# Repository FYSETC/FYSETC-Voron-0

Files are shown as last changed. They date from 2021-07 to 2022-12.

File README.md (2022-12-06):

# FYSETC-Voron-0.1

This is a project from the VORON community, VORON 0.1. We made a little upgrade and improvement on the basis of this project, and provided a complete set of information. Thanks to the open source materials and support provided by the VORON community, and hope you like it. You can find Voron official information below.

1.VORON 0.1 Official website?¼šhttps://vorondesign.com/voron0.1

2.VORON 0.1 Official Github?¼šhttps://github.com/VoronDesign/Voron-0

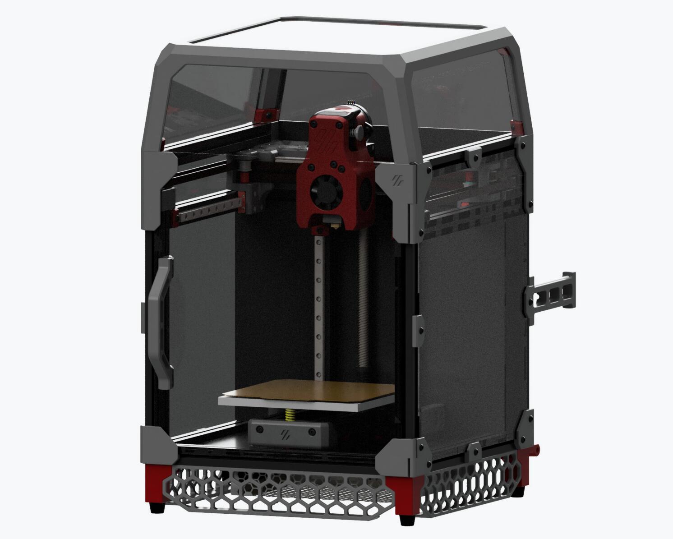
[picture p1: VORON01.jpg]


## 1. Kit advantages:

1?¼‰Using a fully enclosed cabinet design, high-precision finishing anodized custom profile frame, exquisite appearance, can support printing high-temperature consumables, such as: ABS, PC, etc.

2?¼‰Print surface: high-quality powder PEI steel plate, good adhesion, flexibility, easy to take molds; platform: MIC6 aluminum finishing, flatness up to 0.05, attached to high-temperature soft magnetic, and additionally designed positioning pillars, which can be fast Place the steel plate in place and not easily move.

3?¼‰We use 150W genuine brand new Meanwell power supply, which can provide a stable and reliable energy source for the machine and make the machine run more stable. The Raspberry Pi uses TOBSUN 5V 10A DC module for power supply. In addition to providing reliable power for the Raspberry Pi, it also facilitates your other power supply needs, such as cool light strips.

4?¼‰Tornado hotend, check the features [here](https://github.com/FYSETC/FYSETC-Voron-0/blob/main/Tornado_hotend.md). (Please installation guide on our [youtube](https://www.youtube.com/watch?v=a5HArBp4h3s))

5?¼‰Provide a complete set of crimped terminal wires, suitable in length, plug and play, and easy to use.

6?¼‰It adopts high-precision anti-rust linear guide, precise position and stable operation

7?¼‰Using gates belt, wear-resistant, non-slip, long life.

8?¼‰The door handle is fixed with screws, which is more firm and reliable.

9?¼‰Imported silicone thermal mattress, high temperature resistance, built-in over-temperature fuse, high power 24V 75W, fast heating.

10?¼‰High-quality motors.

11?¼‰The use of a 3:1 reduction ratio extruder can increase the extrusion force of the large distance, ensure the smooth and effective extrusion of the consumables, and improve the printing quality.

12?¼‰Use Klipper firmware
Running on [Cheetah V1.2b](https://github.com/FYSETC/FYSETC-Cheetah) (On kit rev 1.0) or [Cheetah v2.0](https://github.com/FYSETC/FYSETC-Cheetah-v2) (On kit rev1.1) and Raspberry Pi 3B+, it can achieve higher printing speed, provide Web control (via WiFi or Ethernet), can connect to a camera, and can be equipped with a 12864 display screen.

## 2. BOM

Check [here](https://github.com/FYSETC/FYSETC-Voron-0/blob/main/BOM.md).

## 3. Modified STLs (2021.07.22)

We update some STLs for the kit. As we found the following issues during the test that 

1.`[a]_Cowling_dragon_x1.stl` fan is difficult to install; 

2.`[a]Mid_Body_Dragon_x1.stl` feed hole is too small; 

3.`Strain_Relief_Spacers_x2.stl` motor uses 20 height; 

4.`Door_Handle_x1 handle.stl` The glue won't stick.

So we modify these STLs base on the originals. You can find them in our `github` or `gitee`.

`[a]_Cowling_dragon_x1.stl` : [github](https://github.com/FYSETC/FYSETC-Voron-0/blob/main/STLs/Toolheads/Mini_Afterburner/Dragon_Toolhead_DD/%5Ba%5D_Cowling_dragon_x1.stl)

`[a]Mid_Body_Dragon_x1.stl`: [github](https://github.com/FYSETC/FYSETC-Voron-0/blob/main/STLs/Toolheads/Mini_Afterburner/Dragon_Toolhead_DD/%5Ba%5D_Mid_Body_Dragon_x1.STL)

`Strain_Relief_Spacers_x2.stl` : [github](https://github.com/FYSETC/FYSETC-Voron-0/blob/main/STLs/Toolheads/Mini_Afterburner/Strain_Relief_Spacers_x2.STL)

`Door_Handle_x1.stl`: [github](https://github.com/FYSETC/FYSETC-Voron-0/blob/main/STLs/Panel_Mounting/Door_Handle_x1.STL)

You can also download these STL files in our `thingiverse` [here](https://www.thingiverse.com/thing:4914152).

## 4. Installation Guide

### 4.1 VORON Assembly manual

Check it [here](https://github.com/VoronDesign/Voron-0/blob/Voron0.1/Manuals/Assembly_Manual_0.1.pdf).

### 4.2 Tornado Hotend installation

Please check it on our [youtube](https://www.youtube.com/watch?v=a5HArBp4h3s).

## 5. Wiring

### 5.1 Rev1.0 kit

Following is our Cheetah v1.2 board wiring diagram for VORON 0.1 rev1.0 kit.

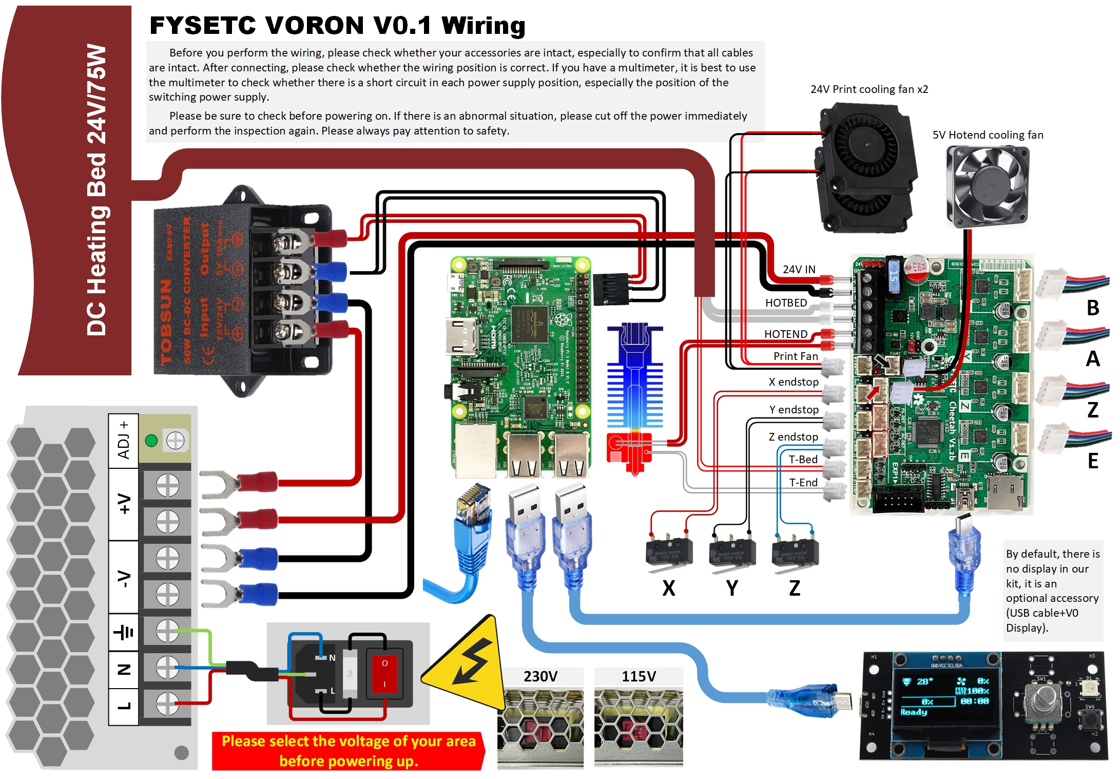
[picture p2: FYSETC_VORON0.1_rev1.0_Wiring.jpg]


We make an example wiring for you, but i think you can do a better job than us. Looking forward to yours, you can share it on VORON discord.



### 5.2 Rev1.1 kit

Following is our Cheetah v2.0 board wiring diagram for VORON 0.1 rev1.1 kit.

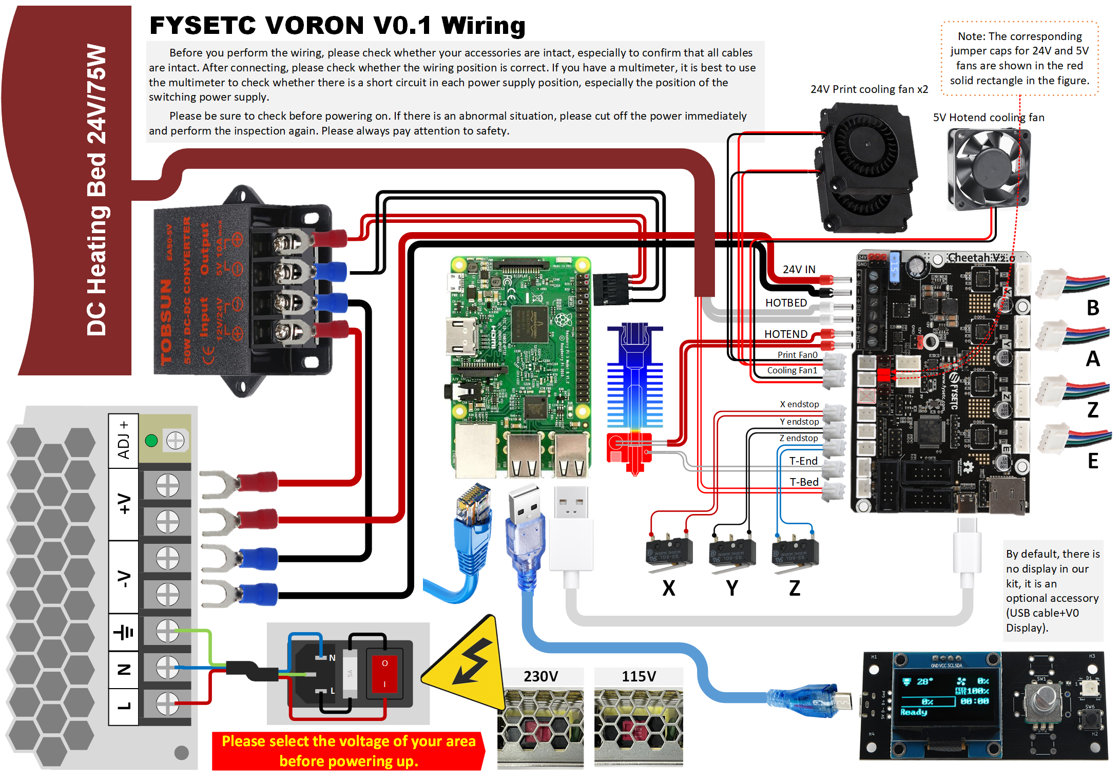
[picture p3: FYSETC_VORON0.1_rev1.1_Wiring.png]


## 6. Firmware&OS

You can check `README.md` in `Firmware&OS` folder beside this `README.md` file [here](https://github.com/FYSETC/FYSETC-Voron-0/tree/main/Firmware&OS). Well we already flashed OS system (on sdcard) and Klipper firmware on Cheetah board for you before the kit leave the factory.

## 7. Community

[Voron community](https://discord.gg/voron)

[FYSETC Facebook group](https://www.facebook.com/groups/238970713918171)

## 8. Buy link

[Aliexpress](https://www.aliexpress.com/item/1005003123492072.html)

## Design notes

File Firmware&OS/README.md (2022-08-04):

# Firmware&OS

## 1. Firmware

### 1.1 Rev 1.0

We use `Cheetah v1.2` motherboard ([github](https://github.com/FYSETC/FYSETC-Cheetah)) for our `Voron-0` rev1.0 kit. And we use `Klipper` firmware. You can get the pre-build firmwares and `printer.cfg` files in folder `rev1.0` next to this `README` file.  In the kit you should find an sdcard with octopi system flashed. After you build your Voron 0.1 machine, you can insert it to the raspberrypi and power up the machine, the machine should work. Remember to connect ethernet cable to raspberrypi and connect Cheetah board to raspberrypi with USB cable.  

#### 1.1.1 Klipper compile

We use the following `make menuconfig` below to compile Klipper. You can check more firmware build information in our Cheetah board github page [here](https://github.com/FYSETC/FYSETC-Cheetah#klipper).

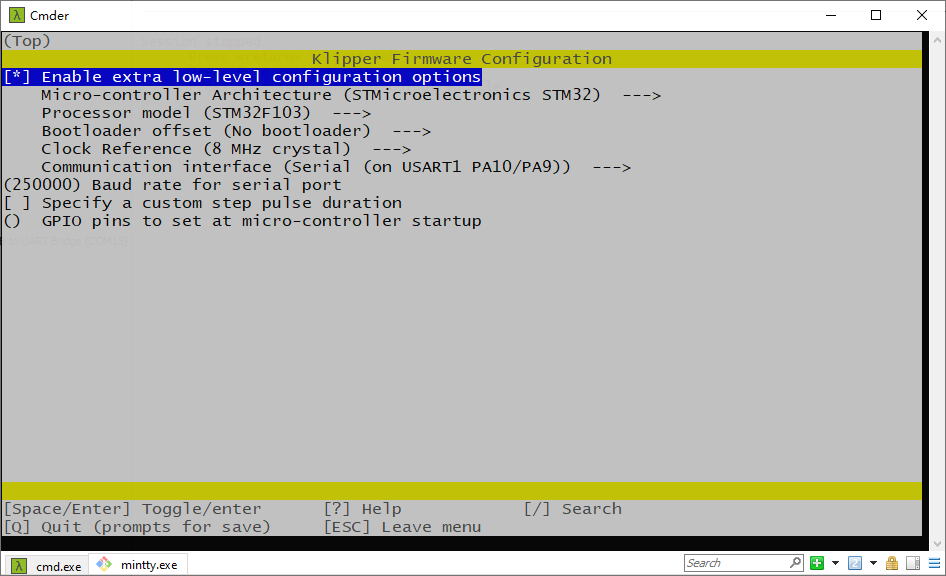
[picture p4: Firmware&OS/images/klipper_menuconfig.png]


#### 1.1.2 How to flash firmware

Well, i don't recommend you to use our pre-build firmwares as klipper firmware always update. I recommend you to compile klipper yours, follow it [here](https://www.klipper3d.org/Installation.html). The prebuild firmwares below just for beginners.

You should power up Cheetah board with 12v/24v power supply first.

##### klipper.bin

If you use our pre-build `klipper.bin` firmware, you can flash the firmware with the command below. This command is also for those who compile klipper yourself, but you need to `cd ~/klpper/out` first. Remember to connect RaspberryPi with usb cable to Cheetah.

```
stm32flash -w klipper.bin -v -i rts,-dtr,dtr /dev/ttyUSB0
```

##### klipper.hex

This is our pre-build firmware in hex format, you can flash it in windows system. 

You can follow the following steps to upload the bootloader.

- Download the flash software in our github https://github.com/FYSETC/STM32Flasher
- Power the board with power supply and connect the board to your PC with USB cable
- Double the click "FlyMcu.exe" software

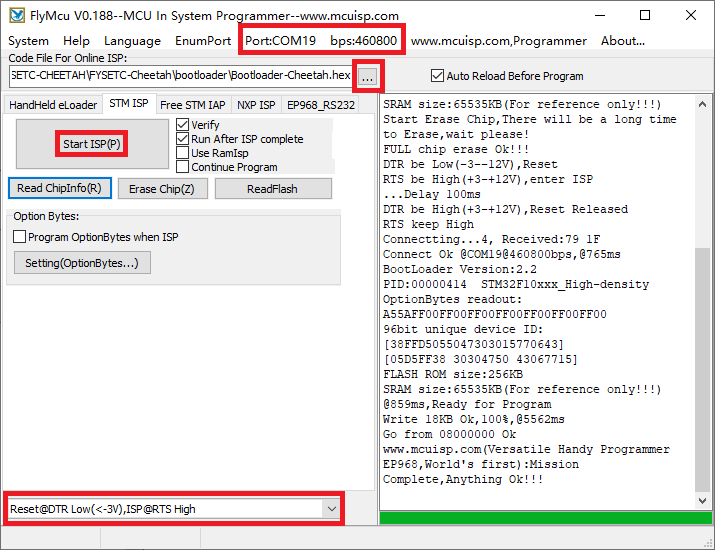
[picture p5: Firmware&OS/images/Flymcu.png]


- Select `Reset@DTR low(<-3v),ISP @RTS High`
- Click "Port" to select the port of your USB
- Select `Bootloader-STM32F103.hex` in the `Code File For Online ISP:` edit box. There is bootloader file named `Bootloader-STM32F103.hex` beside this `README` file.
- At last, click `Start ISP(p)` button to upload the firmware.

#### 1.1.3 printer.cfg

We provide you an example `printer.cfg` in folder `rev1.0` beside this `README` file.

### 1.2 Rev 1.1

We use `Cheetah v2.0` motherboard ([github](https://github.com/FYSETC/FYSETC-Cheetah)) for our `Voron-0` rev1.1 kit. And we use `Klipper` firmware. You can get the pre-build firmwares and `printer.cfg` files in `rev1.1` beside this `README` file.  

#### 1.2.1 Klipper compile

We use the following `make menuconfig` below to compile Klipper. You can check more firmware build information in our Cheetah v2 board github page [here](https://github.com/FYSETC/FYSETC-Cheetah-v2#52-klipper).

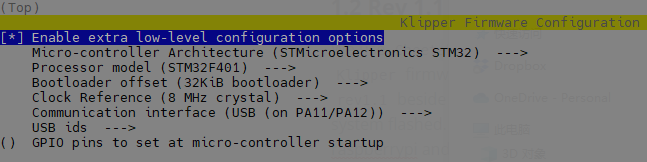
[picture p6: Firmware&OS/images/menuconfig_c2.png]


#### 1.2.2 How to flash firmware

Well, i don't recommend you to use our pre-build firmwares as klipper firmware always update. I recommend you to compile klipper yourself, follow it [here](https://www.klipper3d.org/Installation.html). The pre-build firmwares below just for beginners.

##### klipper.hex

This is our pre-build firmware hex format, follow the instruction [here](https://github.com/FYSETC/FYSETC-Cheetah-v2#533-upload-the-firmwarewindows-dfu) to flash it.

*Note: It is hex file, you don't need to set `Start address` option when using STM32CubeProgrammer.*

Check the klipper version below



##### klipper.bin

32k offset firmware, use the command below to upload the firmware (linux based OS).

```
dfu-util -R -a 0 -s 0x08008000:leave -D klipper.bin
```

#### 1.2.3 printer.cfg

We provide you an example `printer.cfg` in folder `rev1.1` beside this `README` file.

## 2. OS

We provide you two OS images choices: Mainsail OS and Octopi OS.

### 2.1 Mainsail OS

This OS image is only for kit rev1.1 and later, you can get the corresponding Mainsail OS here([1.Dropbox](https://www.dropbox.com/s/669lq3r6z1t4mzo/voron0.1_rpi_cheetah2.0_mainsail.zip?dl=0) [2.百度云盘](https://pan.baidu.com/s/1RYXrs2E_AEZvYQI9CqWZ3w) 提取码：9527) .

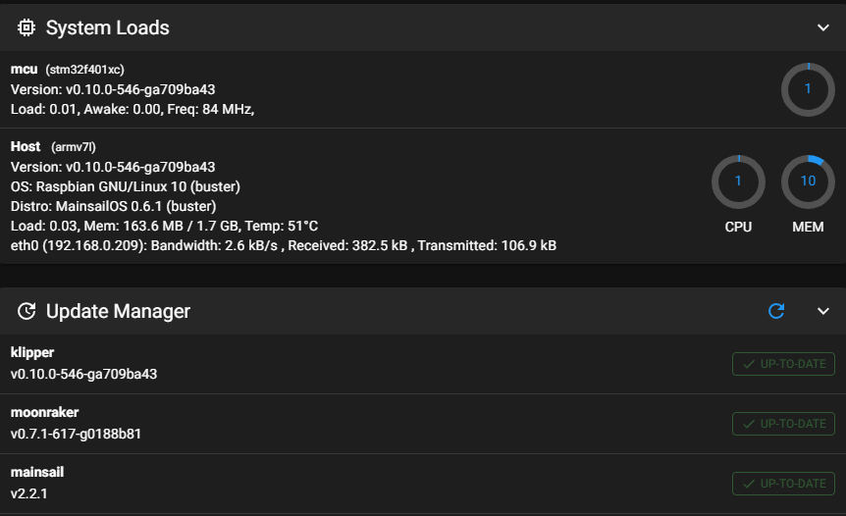
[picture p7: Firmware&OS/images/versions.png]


### 2.2 Octopi OS

If your kit version is rev1.0, then your cheetah board version is 1.2, you can get the corresponding Octopi OS here([1.Dropbox](https://www.dropbox.com/s/o599ni65a6fd2by/voron0.1-cheetah1.2-octopi0.18-octoprint1.6.1-klipper-final.img?dl=0) [2.百度云盘](https://pan.baidu.com/s/1epDDUFP4t6gNax9Bxs07-w) 提取码：1357) . If your kit version is rev1.1, then your cheetah board version is 2.0, and you can get the corresponding Octopi  OS image here([1.Dropbox](https://www.dropbox.com/s/smtbososhue4zym/voron0.1-cheetah2.0-octopi0.18-octoprint1.7.2-klipper.img?dl=0) [2.百度云盘](https://pan.baidu.com/s/12OQ6AqPryXO6TYDF16cSlw ) 提取码：YYDS).

You can login in Octoprint with the following account and password.

```
Account: FYSETC
Password: 12345678
```

### 2.3 How to flash OS image

Before flash, you need an SD card , minimum requirement of SD card capacity is 8G. Please prepare that first. And then you can use this software [here](https://www.balena.io/etcher/) to install. Well that are so many OS flash tool that you can use. And there are a lot of tutorial if you google `how to flash os image`.

### 2.4 SSH account and password

OS SSH account and password

```
Account: pi
Password: raspberry
```

## 3. V0_Display

If you want to install V0_Display to the machine, you should update its firmware first. Please follow `README` in [github](https://gitee.com/fysetc/Voron-Hardware/blob/master/V0_Display/Documentation/Setup_and_Flashing_Guide.md) or [gitee](https://github.com/VoronDesign/Voron-Hardware/blob/master/V0_Display/Documentation/Setup_and_Flashing_Guide.md).

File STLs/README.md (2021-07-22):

# FYSETC-Voron-0.1-STL-update
FYSETC VORON 0.1 STL update part:

Why update: The official original found during the test that 1.[a]_Cowling_dragon_x1 fan is difficult to install; 2.[a]_Mid_Body_x1 feed hole is too small; 3.Strain_Relief_Spacers_x2 motor uses 20 height; 4.Door_Handle_x1 handle The glue won't stick.

1.[a]_Cowling_dragon_x1

2.[a]_Mid_Body_x1

3.Strain_Relief_Spacers_x2

4.Door_Handle_x1

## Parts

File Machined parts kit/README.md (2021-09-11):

# Machined parts kit

If you buy our machined parts kit, you need following STLs to finish your build.

```
Hotbed_wire_harness_clamp.STL
```

```
rear_right_foot.STL
```

Also you can find them in our Thingiverse: https://www.thingiverse.com/thing:4961615

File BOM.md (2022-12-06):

# Package list 

## Revision 1.0

| Index | Sort | Component | Qty | Note |
| ----- | :--- | --- | --- | --- |
| 1 | Fasteners | Voron V0.1 fasteners Pack | 1 SET  | |
| 2 | Extruder Hardware | BMG Extruder gear kit(Includes all accessories) | 1 SET  | |
| 3 | Frame | Voron 0.1 1515 aluminum extrusion profile frame kit | 19 PCS | |
| 4 | Electronics | Meanwell LRS-150-24 | 1 PC | |
| 5 | Electronics | Buck converter - 24V to 5V | 1 PC | |
| 6 | Electronics | FYSETC  cheetah 1.2 | 1 PC | |
| 7 | Electronics | Raspberry Pi 3B+ | 1 PC | |
| 8 | Electronics | MicroSD Card 8G | 1 PC | |
| 9 | Electronics | NEMA14 Stepper Motor 40Ncm 35HSH7402-24B-400A(check [here](https://github.com/FYSETC/FYSETC-MOTORS/tree/main/35HSH7402-24B-400A)) | 2 PCS  | |
| 10 | Electronics | NEMA17 Stepper Motor (34mm max) with integrated lead screw 200mm T8x8 42HSC1404B-200N8(check [here](https://github.com/FYSETC/FYSETC-MOTORS/tree/main/42HSC1404B-200N8)) | 1 PC | |
| 11 | Electronics | NEMA14 36mm round pancake Stepper Motor with 10 tooth spur gear G36HSY4407-6D-550(check [here](https://github.com/FYSETC/FYSETC-MOTORS/tree/main/G36HSY4407-6D-550)) | 1 PCS  | |
| 12 | Electronics | 3010 blower fans 24V | 1 PC | |
| 13 | Electronics | 3007 axial fan 5V (min 3.5CFM) | 1 PC | |
| 14 | Electronics | Micro Switch（With wire） | 3 PCS  | |
| 15 | Electronics | C13 Power Cord | 1 PC | |
| 16 | Electronics | AC Inlet （ With Fuse ） | 1 SET  | |
| 17 | Electronics | Tornodo hotend（ Both all-metal and PTFE heatbreak included） | 1 PC | |
| 18 | Electronics | 24V Heater Cartridge (slim wires) | 1 PC | |
| 19 | Electronics | Thermistor for your hotend of choice | 1 PC | |
| 20 | Electronics | VHB tape (20mm) | 1 PC | |
| 21 | Cables | VORON 0.1 cables kit（All cables are connected to the terminals，Plug and play） | 1 SET  | |
| 22 | Cables | 2mmx120mm zip ties | 20 PCS | |
| 23 | Cables | Network cable | 1 PC | |
| 24 | Motion | F623-RS Bearing | 24 PCS | |
| 25 | Motion | MGN7H Linear Rail with Carriage (150mm) | 5 PCS  | |
| 26 | Motion | GT2 20T (6mm wide) (5mm bore) | 2 PCS  | |
| 27 | Motion | GATES-LL-GT2 Open Belt 6mm (3 meters) | 1 PC | |
| 28 | Motion | T8 flange Nut 8mm Lead --anti-backlash | 1 PC | |
| 29 | Buildplate | Aluminum Build Plate (MIC6) 120x120mm | 1 PC | Positionable steel plate like prusa |
| 30 | Buildplate | Silicone DC 24V Heater 100x100mm 75W （Faster heating rate，Fuse inside） | 1 PC | |
| 31 | Buildplate | Yellow die springs 8x4x20mm | 3 PCS  | |
| 32 | Buildplate | PEI Powder Coated Spring Steel Flex Buildplate 120x120mm | 1 PC | |
| 33 | Buildplate | Magnetic sheet for spring steel plate 120x120mm | 1 PC | |
| 34 | Panels | VORON 0.1 Acrylic Panels kit | 1 SET  | |
| 35 | Bowden | Bowden Fitting ECAS04 | 1 PC | |
| 36 | Bowden | Bowden Tubing 4mmOD 1.9mmID (1.5 meter) | 1 PC | |
| 37 | Misc | Little Rubber Feet (14x11x9mm) | 4 PCS  | |
| 38 | Misc | 6mm x 3mm Round Neodymium Magnets | 8 PCS  | |
| 39 | Misc | Weaving casing φ8mm length 300mm | 1 SET  | Replace one tank chain |
| 40 | Misc | Weaving casing φ8mm length 350mm | 1 SET  | |
| 41 | Misc | FYSETC label | 1 PC | |
| 42 | Tools | Cutting pliers | 1 SET  | |
| 43 | Tools | Hexagonal wrenchs | 1 PC | |
| 44 | Tools | Thermal silica | 1 PC | |
| 45 | Tools | FYSETC VORON V0.1 Wiring manual | 1 SET  | |

## Revision 1.1

| Index | Sort | Component | Qty | Note |
| ----- | :--- | --- | --- | --- |
| 1 | Fasteners | Voron V0.1 fasteners Pack | 1 SET  | v1.1 add Motor Spacer |
| 2 | Extruder Hardware | BMG Extruder gear kit(Includes all accessories) | 1 SET  | |
| 3 | Frame | Voron 0.1 1515 aluminum extrusion profile frame kit | 19 PCS | |
| 4 | Electronics | Meanwell LRS-150-24 | 1 PC | |
| 5 | Electronics | Buck converter - 24V to 5V | 1 PC | |
| 6 | Electronics | FYSETC  cheetah 2.0 | 1 PC | v1.1 Upgrade to 2.0 |
| 7 | Electronics | Raspberry Pi 3B+ | 1 PC | |
| 8 | Electronics | MicroSD Card 8G | 1 PC | |
| 9 | Electronics | NEMA14 Stepper Motor 40Ncm 35HSH7402-24B-400A(check [here](https://github.com/FYSETC/FYSETC-MOTORS/tree/main/35HSH7402-24B-400A)) Teflon wire | 2 PCS  | v1.1 upgraded to Teflon line |
| 10 | Electronics | NEMA17 Stepper Motor (34mm max) with integrated lead screw 200mm T8x8 42HSC1404B-200N8(check [here](https://github.com/FYSETC/FYSETC-MOTORS/tree/main/42HSC1404B-200N8)) Teflon wire | 1 PC | v1.1 upgraded to Teflon line |
| 11 | Electronics | NEMA14 36mm round pancake Stepper Motor with 10 tooth spur gear G36HSY4407-6D-550(check [here](https://github.com/FYSETC/FYSETC-MOTORS/tree/main/G36HSY4407-6D-550)) Teflon wire | 1 PCS  | v1.1 upgraded to Teflon line |
| 12 | Electronics | 3010 blower fans 24V | 1 PC | v1.1 upgraded to Teflon line |
| 13 | Electronics | 3007 axial fan 5V (min 3.5CFM) | 1 PC | v1.1 upgraded to Teflon line |
| 14 | Electronics | Micro Switch（With wire） | 3 PCS  | v1.1 upgraded to Teflon line |
| 15 | Electronics | C13 Power Cord | 1 PC | |
| 16 | Electronics | AC Inlet （ With Fuse ） | 1 SET  | |
| 17 | Electronics | Tornodo hotend（ Both all-metal and PTFE heatbreak included） | 1 PC | |
| 18 | Electronics | 24V Heater Cartridge (slim wires) | 1 PC | |
| 19 | Electronics | Thermistor for your hotend of choice | 1 PC | |
| 20 | Electronics | VHB tape (20mm) | 1 PC | |
| 21 | Cables | VORON 0.1 cables kit（All cables are connected to the terminals，Plug and play） | 1 SET  | v1.1 upgraded to Teflon line |
| 22 | Cables | 2mmx120mm zip ties | 20 PCS | |
| 23 | Cables | Network cable | 1 PC | |
| 24 | Cables | Type-C line | 1 PC | v1.1 upgraded to elbow |
| 25 | Motion | F623-RS Bearing | 24 PCS | |
| 26 | Motion | MGN7H Linear Rail with Carriage (150mm) | 5 PCS  | |
| 27 | Motion | GT2 20T (6mm wide) (5mm bore) | 2 PCS  | |
| 28 | Motion | GATES-LL-GT2 Open Belt 6mm (3 meters) | 1 PC | |
| 29 | Motion | T8 flange Nut 8mm Lead --anti-backlash | 1 PC | |
| 30 | Buildplate | Aluminum Build Plate (MIC6) 120x120mm | 1 PC | Positionable steel plate like prusa |
| 31 | Buildplate | Silicone DC 24V Heater 100x100mm 75W （Faster heating rate，Fuse inside） | 1 PC | |
| 32 | Buildplate | Thermal Fuse (125C) | 1 PC | |
| 33 | Buildplate | Yellow die springs 8x4x20mm | 3 PCS  | |
| 34 | Buildplate | PEI Powder Coated Spring Steel Flex Buildplate 120x120mm | 1 PC | |
| 35 | Buildplate | Magnetic sheet for spring steel plate 120x120mm | 1 PC | |
| 36 | Panels | VORON 0.1 Acrylic Panels kit | 1 SET  | |
| 37 | Bowden | Bowden Fitting ECAS04 | 2 PC | v1.1 added 1PC |
| 38 | Bowden | Bowden Tubing 4mmOD 1.9mmID (1.5 meter) | 1 PC | |
| 39 | Misc | Tank Chain 7x7mm | 1 PC | v1.1 added |
| 39 | Misc | Little Rubber Feet (14x11x11mm) | 4 PCS  | v1.1 `2mm` taller than v1.0 |
| 40 | Misc | XH2.54 2/3/4 Pin Plastic shell | 1 SET  | v1.1 added |
| 41 | Misc | 6mm x 3mm Round Neodymium Magnets | 8 PCS  | |
| 42 | Misc | Weaving casing φ8mm length 300mm | 1 SET  | |
| 43 | Misc | Weaving casing φ8mm length 350mm | 1 SET  | |
| 44 | Misc | FYSETC label | 1 PC | |
| 45 | Tools | Cutting pliers | 1 SET  | |
| 46 | Tools | Hexagonal wrenchs | 1 PC | |
| 47 | Tools | Thermal silica | 1 PC | |
| 48 | Tools | FYSETC VORON V0.1 Wiring manual | 1 SET  | |
## Revision 1.2

| Index | Sort | Component | Qty | Note |
| ----- | :--- | --- | --- | --- |
| 1 | Fasteners | Voron V0.1 fasteners Pack | 1 SET  | v1.1 add Motor Spacer |
| 2 | Extruder Hardware | BMG Extruder gear kit(Includes all accessories) | 1 SET  | |
| 3 | Frame | Voron 0.1 1515 aluminum extrusion profile frame kit | 19 PCS | |
| 4 | Electronics | Meanwell LRS-150-24 | 1 PC | |
| 5 | Electronics | Buck converter - 24V to 5V | 1 PC | |
| 6 | Electronics | FYSETC  cheetah 2.0 | 1 PC | v1.1 Upgrade to 2.0 |
| 7 | Electronics | Raspberry Pi 4B 2GB | 1 PC | V1.2 Optional |
| 8 | Electronics | MicroSD Card 8G | 1 PC | |
| 9 | Electronics | NEMA14 Stepper Motor 40Ncm 35HSH7402-24B-400A(check [here](https://github.com/FYSETC/FYSETC-MOTORS/tree/main/35HSH7402-24B-400A)) Teflon wire | 2 PCS  | v1.1 upgraded to Teflon line |
| 10 | Electronics | NEMA17 Stepper Motor (34mm max) with integrated lead screw 200mm T8x8 42HSC1404B-200N8(check [here](https://github.com/FYSETC/FYSETC-MOTORS/tree/main/42HSC1404B-200N8)) Teflon wire | 1 PC | v1.1 upgraded to Teflon line |
| 11 | Electronics | NEMA14 36mm round pancake Stepper Motor with 10 tooth spur gear G36HSY4407-6D-550(check [here](https://github.com/FYSETC/FYSETC-MOTORS/tree/main/G36HSY4407-6D-550)) Teflon wire | 1 PCS  | v1.1 upgraded to Teflon line |
| 12 | Electronics | 3010 blower fans 24V | 1 PC | v1.1 upgraded to Teflon line |
| 13 | Electronics | 3007 axial fan 5V (min 3.5CFM) | 1 PC | v1.1 upgraded to Teflon line |
| 14 | Electronics | Micro Switch（With wire） | 3 PCS  | v1.1 upgraded to Teflon line |
| 15 | Electronics | C13 Power Cord | 1 PC | |
| 16 | Electronics | AC Inlet （ With Fuse ） | 1 SET  | v1.2 Wiring color changes |
| 17 | Electronics | Tornodo hotend（ Both all-metal and PTFE heatbreak included） | 1 PC | |
| 18 | Electronics | 24V Heater Cartridge (slim wires) | 1 PC | |
| 19 | Electronics | Thermistor for your hotend of choice | 1 PC | |
| 20 | Electronics | VHB tape (20mm) | 1 PC | |
| 21 | Cables | VORON 0.1 cables kit（All cables are connected to the terminals，Plug and play，Label buckle） | 1 SET  | v1.1 upgraded to Teflon line  v1.2 add Label buckle |
| 22 | Cables | 2mmx120mm zip ties | 20 PCS | |
| 23 | Cables | Network cable | 1 PC | |
| 24 | Cables | Type-C line | 1 PC | v1.1 upgraded to elbow |
| 25 | Motion | F623-RS Bearing | 24 PCS | |
| 26 | Motion | MGN7H Linear Rail with Carriage (150mm) | 5 PCS  | |
| 27 | Motion | GT2 20T (6mm wide) (5mm bore) | 2 PCS  | |
| 28 | Motion | GATES-LL-GT2 Open Belt 6mm (3 meters) | 1 PC | |
| 29 | Motion | T8 flange Nut 8mm Lead --anti-backlash | 1 PC | |
| 30 | Buildplate | Aluminum Build Plate (MIC6) 120x120mm | 1 PC | Positionable steel plate like prusa |
| 31 | Buildplate | Silicone DC 24V Heater 100x100mm 75W （Faster heating rate，Fuse inside） | 1 PC | |
| 32 | Buildplate | Thermal Fuse (125C) | 1 PC | |
| 33 | Buildplate | Yellow die springs 8x4x20mm | 3 PCS  | |
| 34 | Buildplate | PEI Powder Coated Spring Steel Flex Buildplate 120x120mm | 1 PC | |
| 35 | Buildplate | Magnetic sheet for spring steel plate 120x120mm | 1 PC | |
| 36 | Panels | VORON 0.1 Acrylic Panels kit | 1 SET  | |
| 37 | Bowden | Bowden Fitting ECAS04 | 2 PC | v1.1 added 1PC |
| 38 | Bowden | Bowden Tubing 4mmOD 1.9mmID (1.5 meter) | 1 PC | |
| 39 | Misc | Tank Chain 7x7mm | 1 PC | v1.1 added |
| 39 | Misc | Little Rubber Feet (14x11x11mm) | 4 PCS  | v1.1 taller than v1.0 |
| 40 | Misc | XH2.54 2/3/4 Pin Plastic shell | 1 SET  | v1.1 added |
| 41 | Misc | 6mm x 3mm Round Neodymium Magnets | 8 PCS  | |
| 42 | Misc | Weaving casing φ8mm length 300mm | 1 SET  | |
| 43 | Misc | Weaving casing φ8mm length 350mm | 1 SET  | |
| 44 | Misc | FYSETC label | 1 PC | |
| 45 | Tools | Cutting pliers | 1 SET  | |
| 46 | Tools | Hexagonal wrenchs | 1 PC | |
| 47 | Tools | Thermal silica | 1 PC | |
| 48 | Tools | FYSETC VORON V0.1 Wiring manual | 1 SET  | |
## Revision 1.3

| Index | Sort | Component | Qty | Note |
| ----- | :--- | --- | --- | --- |
| 1 | Fasteners | Voron V0.1 fasteners Pack | 1 SET  | v1.1 add Motor Spacer |
| 2 | Extruder Hardware | BMG Extruder gear kit(Includes all accessories) | 1 SET  | |
| 3 | Frame | Voron 0.1 1515 aluminum extrusion profile frame kit | 19 PCS | |
| 4 | Electronics | Meanwell LRS-150-24 | 1 PC | |
| 5 | Electronics | Buck converter - 24V to 5V | 1 PC | |
| 6 | Electronics | FYSETC  cheetah 2.0 | 1 PC | v1.1 Upgrade to 2.0 |
| 7 | Electronics | Raspberry Pi 4B 2GB | 1 PC | V1.2 Optional |
| 8 | Electronics | MicroSD Card 8G | 1 PC | |
| 9 | Electronics | NEMA14 Stepper Motor 40Ncm 35HSH7402-24B-400A(check [here](https://github.com/FYSETC/FYSETC-MOTORS/tree/main/35HSH7402-24B-400A)) Teflon wire | 2 PCS  | v1.1 upgraded to Teflon line |
| 10 | Electronics | NEMA17 Stepper Motor (34mm max) with integrated lead screw 200mm T8x8 42HSC1404B-200N8(check [here](https://github.com/FYSETC/FYSETC-MOTORS/tree/main/42HSC1404B-200N8)) Teflon wire | 1 PC | v1.1 upgraded to Teflon line |
| 11 | Electronics | NEMA14 36mm round pancake Stepper Motor with 10 tooth spur gear G36HSY4407-6D-550(check [here](https://github.com/FYSETC/FYSETC-MOTORS/tree/main/G36HSY4407-6D-550)) Teflon wire | 1 PCS  | v1.1 upgraded to Teflon line |
| 12 | Electronics | 3010 blower fans 24V | 1 PC | v1.1 upgraded to Teflon line |
| 13 | Electronics | 3007 axial fan 5V (min 3.5CFM) | 1 PC | v1.1 upgraded to Teflon line |
| 14 | Electronics | Micro Switch（With wire） | 3 PCS  | v1.1 upgraded to Teflon line |
| 15 | Electronics | C13 Power Cord | 1 PC | |
| 16 | Electronics | AC Inlet （ With Fuse ） | 1 SET  | v1.2 Wiring color changes |
| 17 | Electronics | Tornodo hotend（ Both all-metal and PTFE heatbreak included） | 1 PC | |
| 18 | Electronics | 24V Heater Cartridge (slim wires) | 1 PC | |
| 19 | Electronics | Thermistor for your hotend of choice | 1 PC | |
| 20 | Electronics | VHB tape (20mm) | 1 PC | |
| 21 | Cables | VORON 0.1 cables kit（All cables are connected to the terminals，Plug and play，Label buckle） | 1 SET  | v1.1 upgraded to Teflon line  v1.2 add Label buckle |
| 22 | Cables | 2mmx120mm zip ties | 20 PCS | |
| 23 | Cables | Network cable | 1 PC | |
| 24 | Cables | Type-C line | 1 PC | v1.1 upgraded to elbow |
| 25 | Motion | F623-RS Bearing | 24 PCS | |
| 26 | Motion | MGN7H Linear Rail with Carriage (150mm) | 5 PCS  | v1.3 upgraded to  Stainless steel |
| 27 | Motion | GT2 20T (6mm wide) (5mm bore) | 2 PCS  | |
| 28 | Motion | GATES-LL-GT2 Open Belt 6mm (3 meters) | 1 PC | |
| 29 | Motion | T8 flange Nut 8mm Lead --anti-backlash | 1 PC | |
| 30 | Buildplate | Aluminum Build Plate (MIC6) 120x120mm | 1 PC | Positionable steel plate like prusa |
| 31 | Buildplate | Silicone DC 24V Heater 100x100mm 75W （Faster heating rate，Fuse inside） | 1 PC | |
| 32 | Buildplate | Thermal Fuse (125C) | 1 PC | |
| 33 | Buildplate | Yellow die springs 8x4x20mm | 3 PCS  | |
| 34 | Buildplate | PEI Powder Coated Spring Steel Flex Buildplate 120x120mm | 1 PC | |
| 35 | Buildplate | Magnetic sheet for spring steel plate 120x120mm | 1 PC | |
| 36 | Panels | VORON 0.1 Acrylic Panels kit | 1 SET  | |
| 37 | Bowden | Bowden Fitting ECAS04 | 2 PC | v1.1 added 1PC |
| 38 | Bowden | Bowden Tubing 4mmOD 1.9mmID (1.5 meter) | 1 PC | |
| 39 | Misc | Tank Chain 7x7mm | 1 PC | v1.1 added |
| 39 | Misc | Little Rubber Feet (14x11x11mm) | 4 PCS  | v1.1 taller than v1.0 |
| 40 | Misc | XH2.54 2/3/4 Pin Plastic shell | 1 SET  | v1.1 added |
| 41 | Misc | 6mm x 3mm Round Neodymium Magnets | 8 PCS  | |
| 42 | Misc | Weaving casing φ8mm length 300mm | 1 SET  | |
| 43 | Misc | Weaving casing φ8mm length 350mm | 1 SET  | |
| 44 | Misc | FYSETC label | 1 PC | |
| 45 | Tools | Cutting pliers | 1 SET  | |
| 46 | Tools | Hexagonal wrenchs | 1 PC | |
| 47 | Tools | Thermal silica | 1 PC | |
| 48 | Tools | FYSETC VORON V0.1 Wiring manual | 1 SET  | |

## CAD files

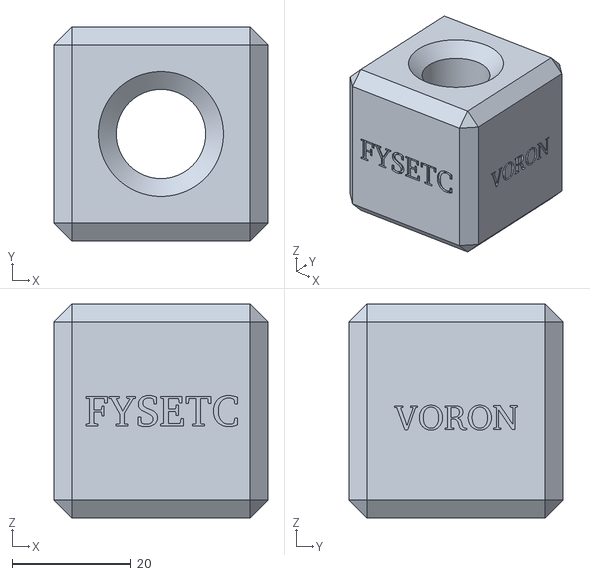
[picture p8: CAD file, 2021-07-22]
FYSETC VORON Cube.STL
36.0 x 36.0 x 36.0

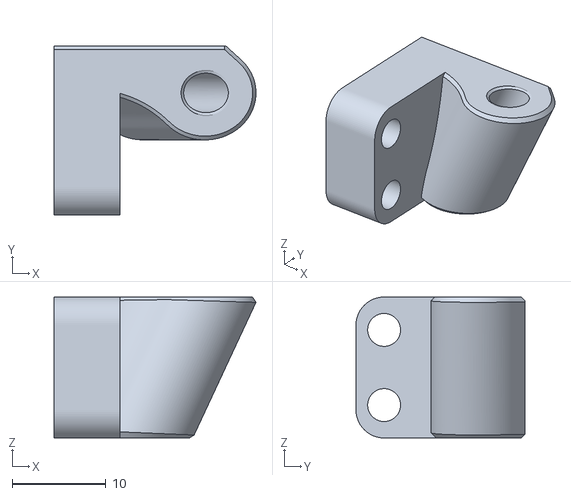
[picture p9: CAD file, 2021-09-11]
Machined parts kit/rear_right_foot.STL
21.5 x 18.0 x 15.0

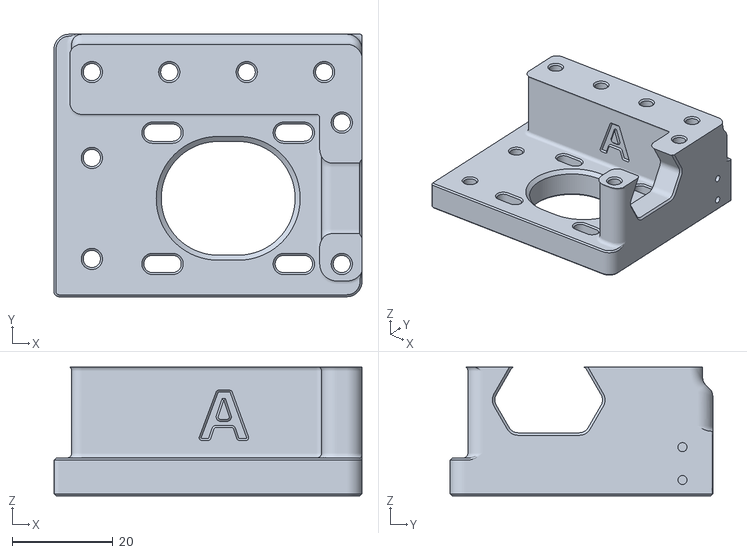
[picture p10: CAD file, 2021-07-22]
STLs/A_Drive_Frame_Lower_x1.stl
61.0 x 52.0 x 25.5

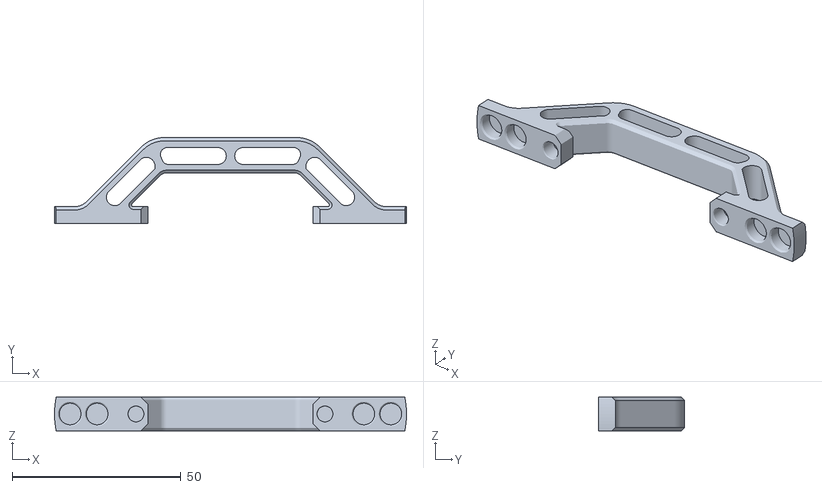
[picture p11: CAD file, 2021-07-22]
STLs/Panel_Mounting/Door_Handle_x1.STL
104.3 x 25.5 x 10.0

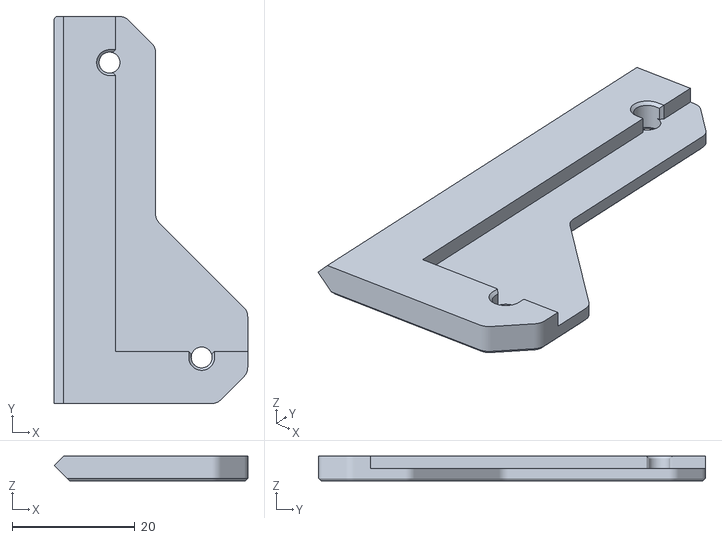
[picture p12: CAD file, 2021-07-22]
STLs/Panel_Mounting/For_2mm_Panels/2mm_Top_Corner_Side_mirror_x1.STL
31.5 x 63.0 x 4.00

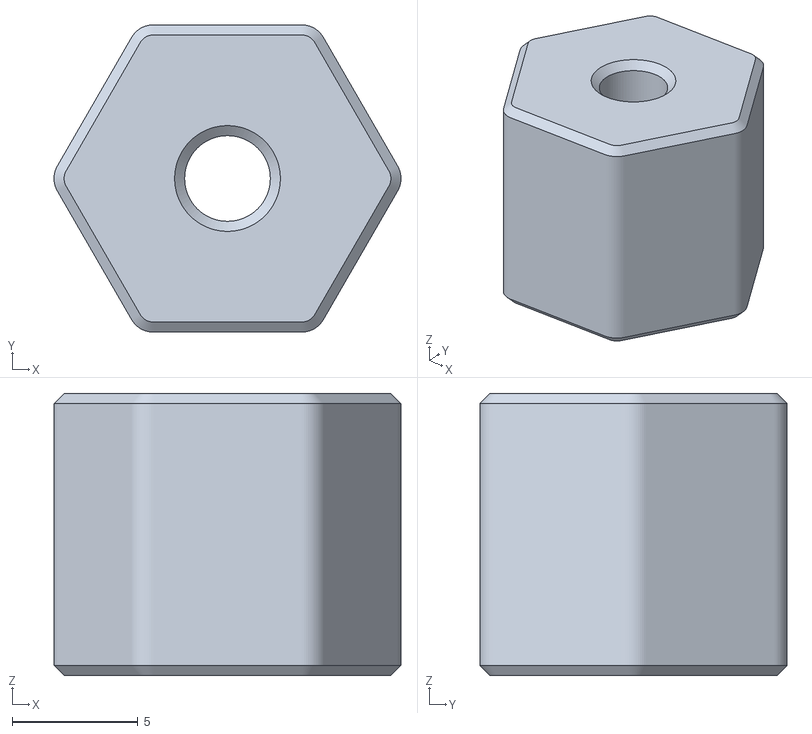
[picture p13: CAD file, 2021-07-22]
STLs/Toolheads/Bowden/[a]_Endstop_Strike_Block_x1.STL
13.8 x 12.2 x 11.2

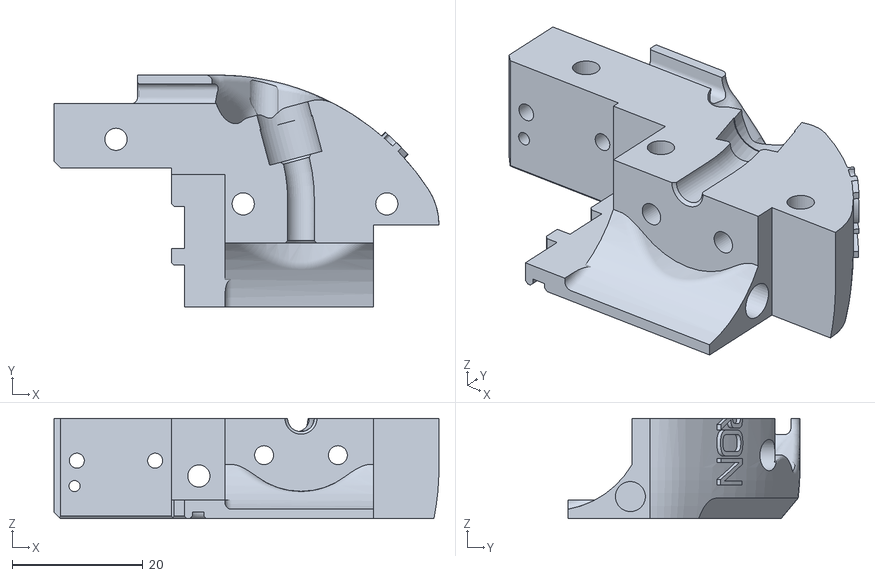
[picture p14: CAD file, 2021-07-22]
STLs/Toolheads/Bowden/Dragon_Toolhead/Toolhead_Right_Dragon_x1.STL
59.0 x 35.6 x 15.4

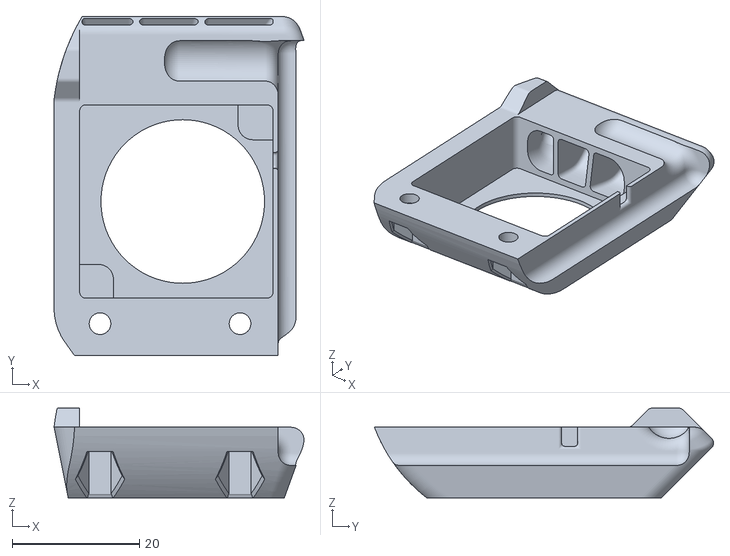
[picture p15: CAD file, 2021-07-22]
STLs/Toolheads/Bowden/Threaded_V6_Toolhead/[a]_Toolhead_Blower_Duct_Right_TV6_x1.STL
39.3 x 53.3 x 14.1

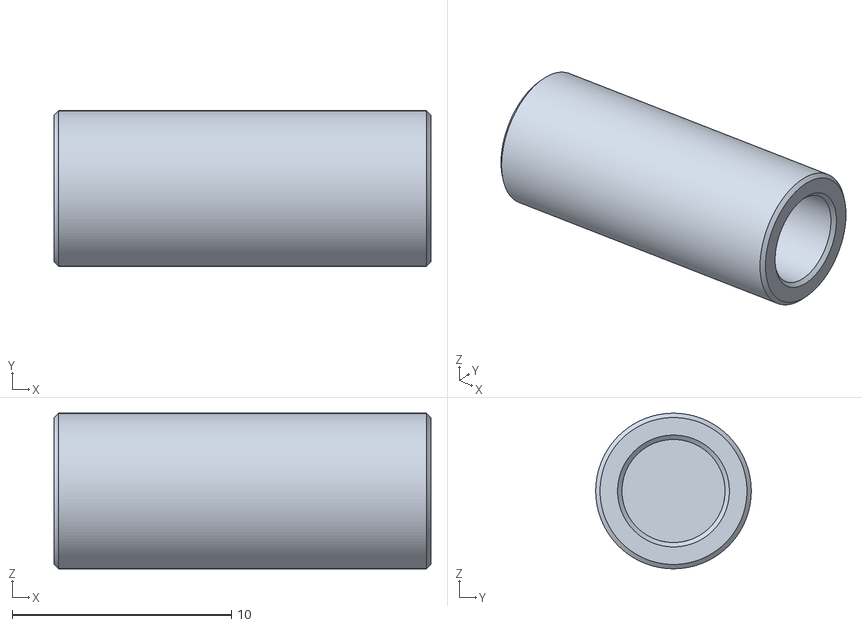
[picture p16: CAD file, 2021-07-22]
STLs/Toolheads/Mini_Afterburner/Strain_Relief_Spacers_x2.STL
17.2 x 7.10 x 7.10

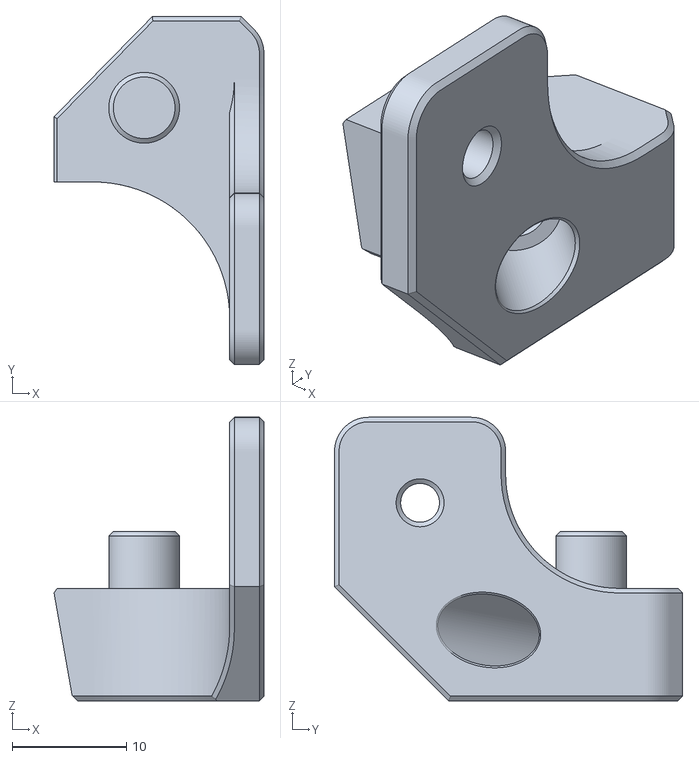
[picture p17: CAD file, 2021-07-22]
STLs/Tophat/Lower_Corner_2_and_4_Clip_x2.STL
18.4 x 30.5 x 24.8

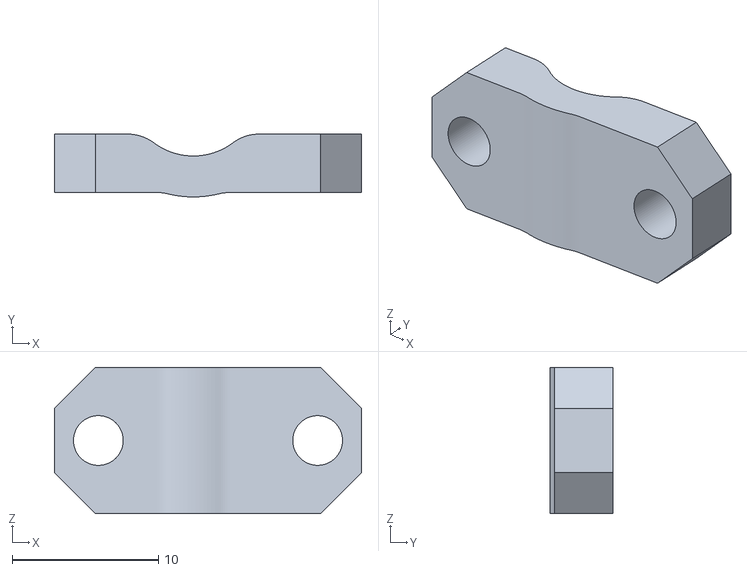
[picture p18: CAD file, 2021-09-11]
Machined parts kit/Hotbed_wire_harness_clamp.STL
21.0 x 4.30 x 10.0

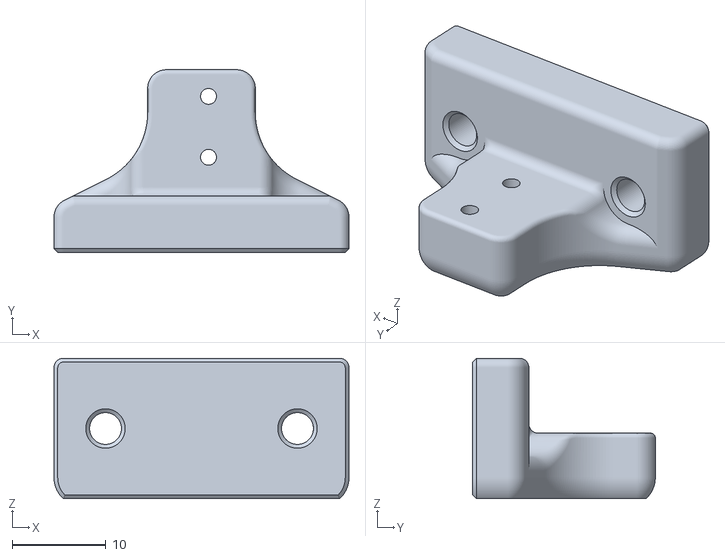
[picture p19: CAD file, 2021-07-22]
STLs/[a]_Z_Endstop_Mount_x1.stl
31.5 x 19.5 x 15.0

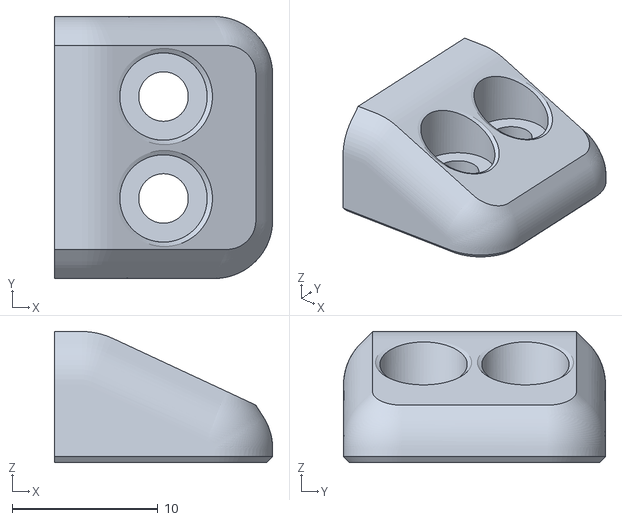
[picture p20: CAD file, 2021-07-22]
STLs/Panel_Mounting/Door_Latch_x2.STL
15.0 x 18.0 x 9.00

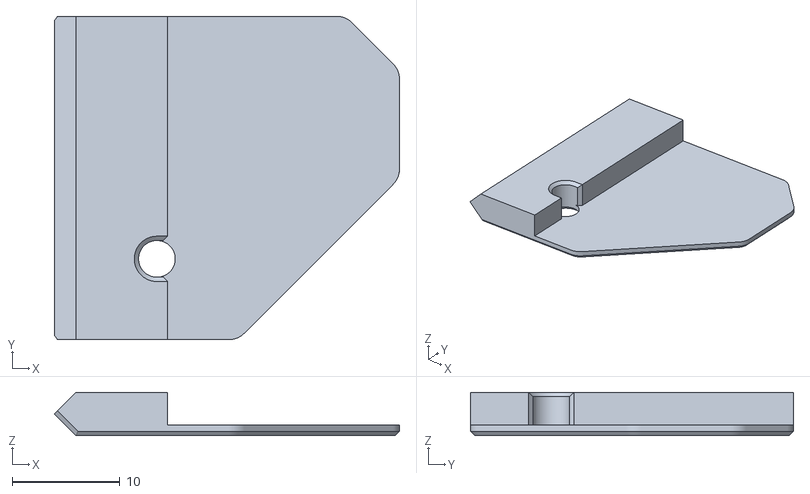
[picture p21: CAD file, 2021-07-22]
STLs/Panel_Mounting/For_2mm_Panels/2mm_Bottom_Corner_Rear_x1.STL
32.0 x 30.0 x 4.00

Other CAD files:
STLs/Toolheads/Bowden/Dragon_Toolhead/Toolhead_Left_Dragon_x1.STL
STLs/Toolheads/Bowden/Threaded_V6_Toolhead/Toolhead_Left_Threaded_V6_x1.STL
STLs/Toolheads/Mini_Afterburner/Cowling_LOGO_ONLY_x1.STL
STLs/Tools/BMG_Shaft_Mod_Spacer_x1.STL
STLs/A_Drive_Frame_Upper_x1.stl
STLs/A_Idler_Lower_x1.stl
STLs/A_Idler_Upper_x1.stl
STLs/B_Drive_Frame_Lower_x1.stl
STLs/B_Drive_Frame_Upper_x1.stl
STLs/B_Idler_Lower_x1.stl
STLs/B_Idler_Upper_x1.stl
STLs/Front_Bed_Mount_x1.stl
STLs/M2_Nut_Adapter_Rotated_x5.stl
STLs/MGN7_Rail_Guide_x2.STL
STLs/PSU_Cover_x1.STL
STLs/Panel_Mounting/For_2mm_Panels/2mm_Bottom_Corner_Front_x1.STL
STLs/Panel_Mounting/For_2mm_Panels/2mm_Bottom_Corner_Rear_mirror_x1.STL
STLs/Panel_Mounting/For_2mm_Panels/2mm_Bottom_Corner_Side_mirror_x1.STL
STLs/Panel_Mounting/For_2mm_Panels/2mm_Bottom_Corner_Side_x2.STL
STLs/Panel_Mounting/For_2mm_Panels/2mm_Hinge_Bottom_A_x1.STL
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

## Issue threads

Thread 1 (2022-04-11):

It appears that the hotend heater and bed heater sensors are reversed on the info for the Cheetah v2.0 board

iwascurious, 2022-04-11:
Recent picture graph shows to plug T-End and T-Bed in the opposite ports which will result in an error found during initial startup.  example here https://github.com/FYSETC/FYSETC-Voron-0/blob/main/FYSETC_VORON0.1_rev1.1_Wiring.png

On Fysetc Wiki for the Cheetah v2.0 the Pin mapping is also reflecting the incorrect info example here https://wiki.fysetc.com/Cheetah_Board_V20/#43-pin-definition

I fixed my issue by switching the T-End and T-Bed sensor connectors on the board. Leaving the same pin mapping as stated in the Fysetc Wiki Cheetah v2.0 list in my Klipper printer.cfg. I can confirm that on my Cheetah v2.0 board the

Temperature
TE0 | PC4 | 24 |  
TB | PC5 | 25

are opposite from what is stated on the board as of the time I posted this.

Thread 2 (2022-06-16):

Please document the reversed headers for non-fysetc 12864 LCD connection

yuriy-yarosh, 2022-06-16:
Example of connecting RepRapDiscount 128x64 with Klipper to Cheetah2

```
# v0_display.cfg

######################################################################
# "RepRapDiscount 128x64 Full Graphic Smart Controller" type displays
######################################################################

[display]
lcd_type: st7920
cs_pin: EXP2_4
sclk_pin: EXP2_5
sid_pin: EXP2_3
click_pin: ^!EXP2_2
encoder_pins: ^EXP1_3, ^EXP1_5
#kill_pin: ^!EXP1_8

[output_pin beeper]
pin: EXP2_1

# Cheetah pinout

# EXP1
# SD-MISO	PA6   22 EXP1_1
# SD-SCK	PA5   21 EXP1_2
# BTN_EN1	PC10  51 EXP1_3
# SD-SS         PA4   20 EXP1_4
# BTN_EN2	PC11  52 EXP1_5
# SD-MOSI	PA7   23 EXP1_6
# SD-DET	PC3   11 EXP1_7
# RESET	        NRST  7	 EXP1_8
# GND	GND	      NA EXP1_9
# 5V	5V	      NA EXP1_10

# EXP2
# BEEP     	PC9 	40	EXP2_1
# BTN_ENC	PC12	53	EXP2_2
# LCD_EN	PB15	36	EXP2_3
# LCD_RS	PB12	33	EXP2_4
# LCD_D4	PB13	34	EXP2_5
# LCD_D5	PB14	35	EXP2_6
# LCD_D6	PB6     58	EXP2_7
# LCD_D7	PB7     59	EXP2_8
# GND	GND	NA	        EXP2_9
# 5V	5V	NA	        EXP2_10

#
# Modified reversed pinout
#
[board_pins]
aliases:
  EXP1_10=<5V>, EXP1_8=<RST>, EXP1_6=PA7,  EXP1_4=PA4,  EXP1_2=PA5,
  EXP1_9=<GND>, EXP1_7=PC3,   EXP1_5=PC11, EXP1_3=PC10, EXP1_1=PA6,

  EXP2_10=<5V>, EXP2_8=PB7, EXP2_6=PB14, EXP2_4=PB12, EXP2_2=PC12,
  EXP2_9=<GND>, EXP2_7=PB6, EXP2_5=PB13, EXP2_3=PB15, EXP2_1=PC9,

# https://github.com/Klipper3d/klipper/blob/master/config/sample-lcd.cfg#L129
# Reversed Plug pin locations

# The following diagram shows the correct location of pin 1
# along with ground and power pins on the EXP1 and EXP2 plugs:
#
#          EXP1:                        EXP2:
#   +-----------------+          +-----------------+
#   |  o  o  o  o  5V |          |  o  o  o  o  o  | -->> EXP1 on Cheetah
#   |  1  o  o  o GND |          |  1  o  o  o GND |
#   +------     ------+          +------     ------+
#
# Reversing the headers is important because STM32 NRST is on EXP1 Cheetah.
#
# Cheetah board has the cutout in the wrong location.
# Make a cutout either on the Cheetah board or on the LCD board directly and reverse the headers.
#
#          EXP1:                        EXP2:
#   +-----|     |-----+          +-----|     |-----+
#   |  o  o  o  o  5V |          |  o  o  o  o  o  | -->> EXP1 on Cheetah
#   |  1  o  o  o GND |          |  1  o  o  o GND |
#   +------     ------+          +------     ------+
#
```

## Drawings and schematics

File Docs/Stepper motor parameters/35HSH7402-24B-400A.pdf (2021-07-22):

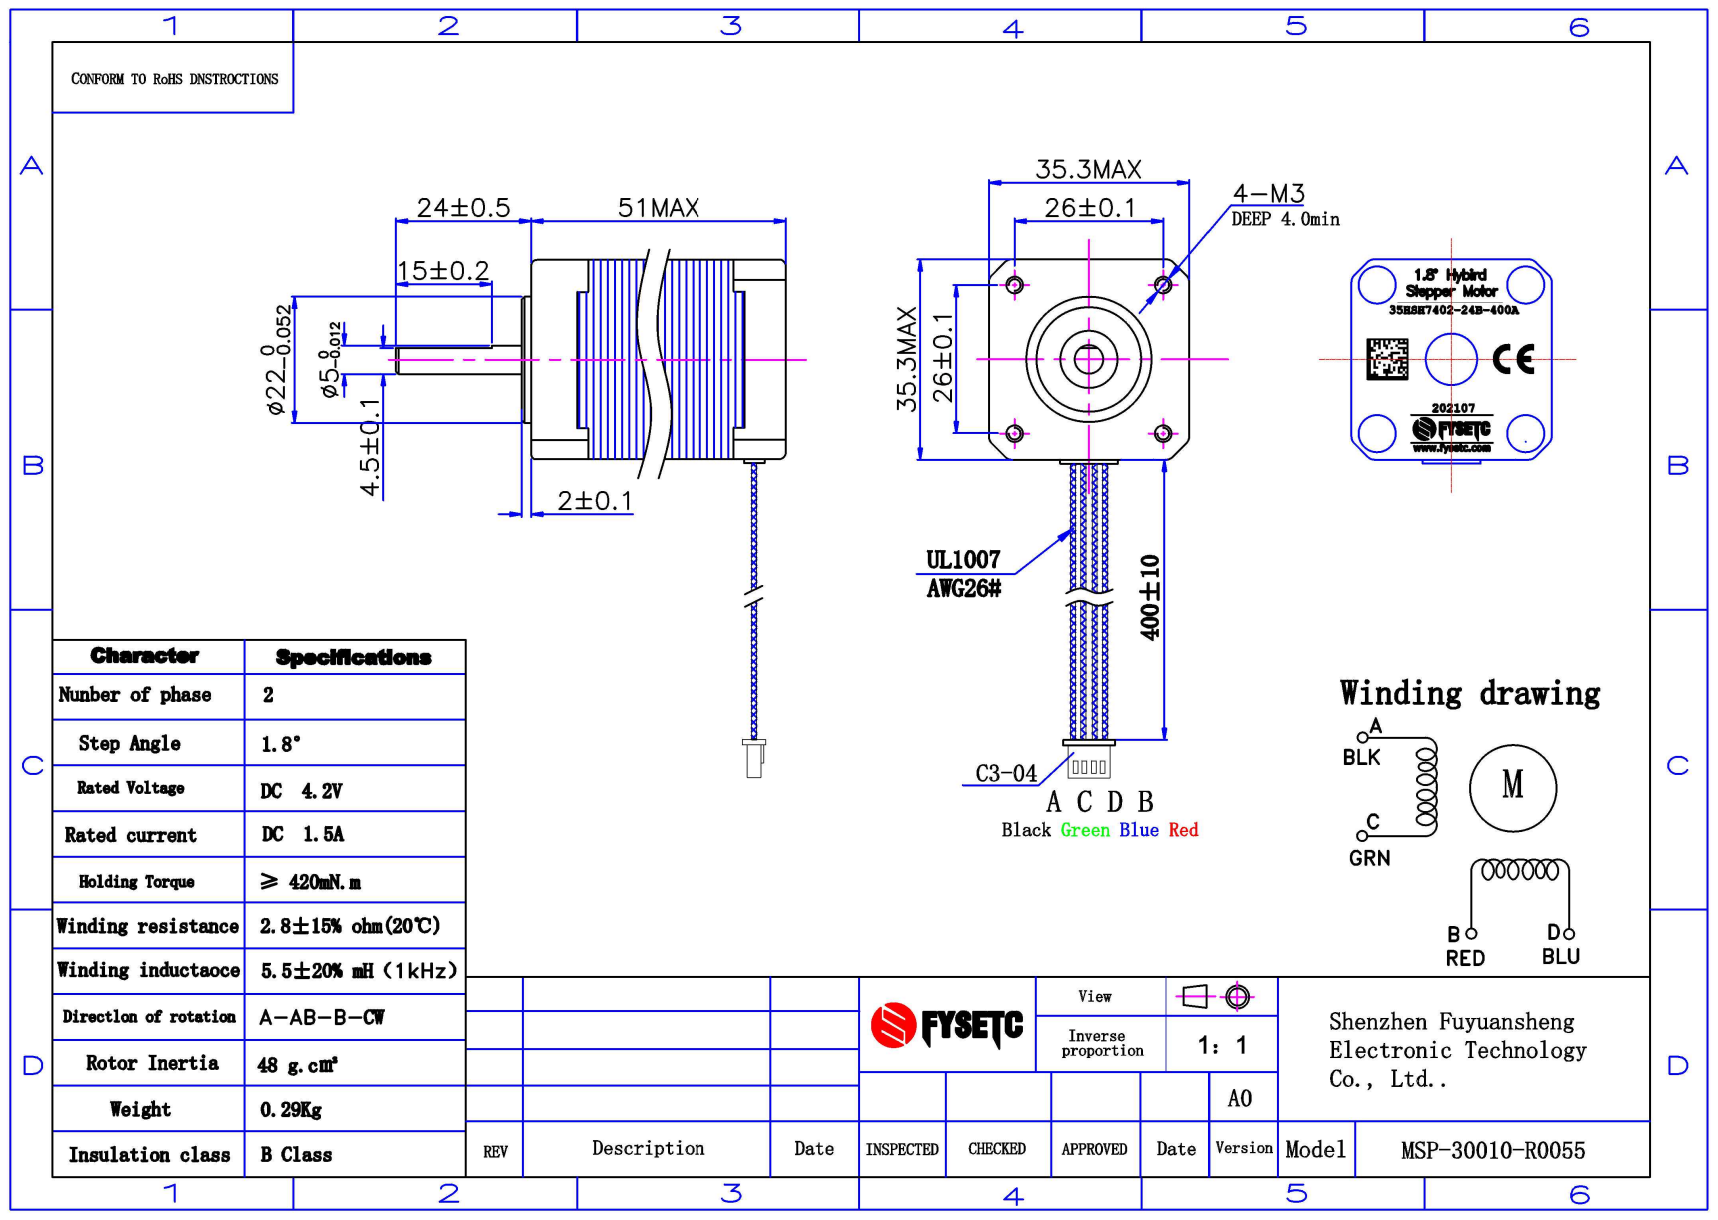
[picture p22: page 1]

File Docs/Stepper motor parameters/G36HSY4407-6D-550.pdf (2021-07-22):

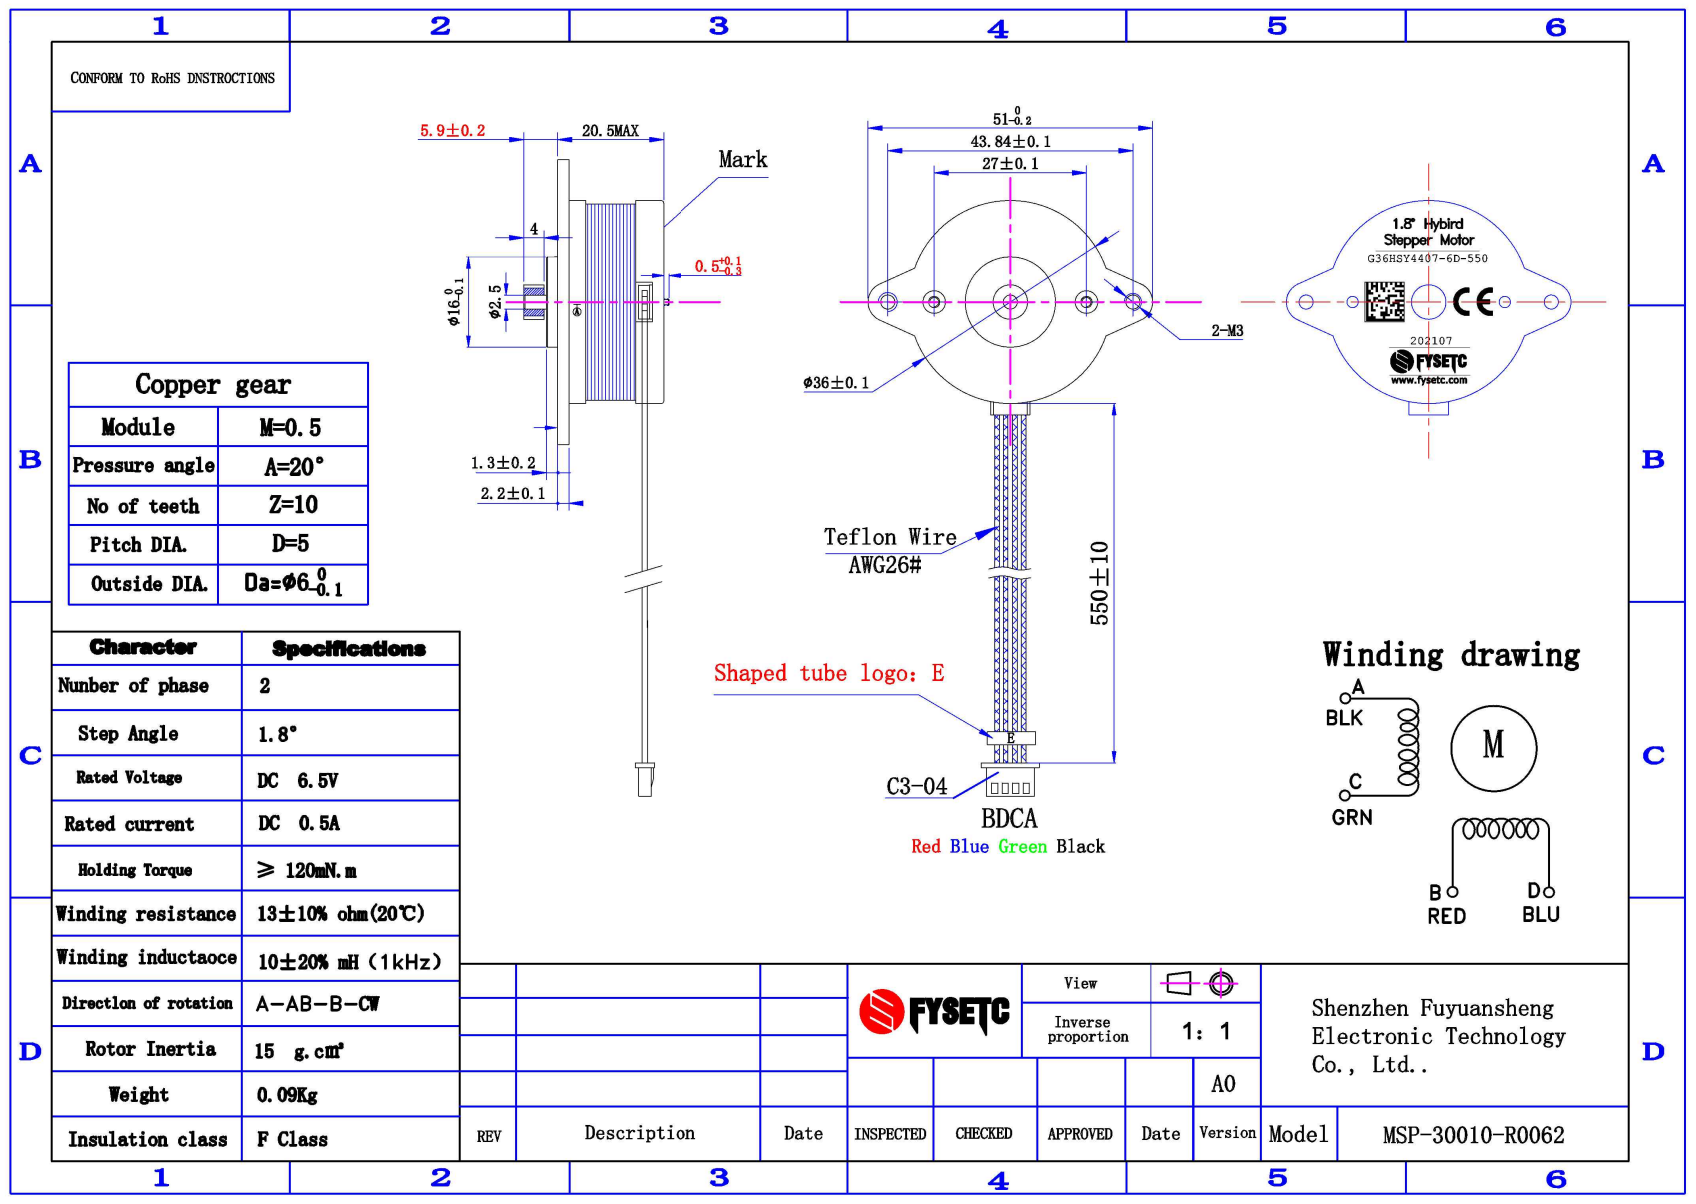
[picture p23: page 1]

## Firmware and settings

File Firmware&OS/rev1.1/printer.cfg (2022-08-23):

# This file contains common pin mappings for the Fysetc Cheetah v2.0
# board. To use this config, the firmware should be compiled for the
# STM32F401 with "No bootloader" and Communication interface USB

# After running "make", run the following command to flash the board:
# dfu-util -R -a 0 -s 0x08000000:leave -D out/klipper.bin

# See docs/Config_Reference.md for a description of parameters.

[mcu]
#####################################################################
#	Obtain mcu value by "ls -l /dev/serial/by-id/" 
#####################################################################
serial: /dev/serial/by-id/usb-Klipper_stm32f401xc_4C004E000C51383336383937-if00

[printer]
kinematics: corexy
max_velocity: 300
max_accel: 4000
max_z_velocity: 15
max_z_accel: 45
square_corner_velocity: 6.0

#####################################################################
#      X/Y Stepper Settings
#####################################################################

[stepper_x]
step_pin: PC0
## Refer to https://docs.vorondesign.com/build/startup/#v0
dir_pin: PC1
enable_pin: !PA8
rotation_distance: 40
microsteps: 16
endstop_pin: ^PB4
full_steps_per_rotation: 200                 # Set to 400 for 0.9¡ã degree stepper motor, 200 is for 1.8¡ã stepper motors
position_endstop: 120
position_max: 120
homing_speed: 20                             # Increase after initial setup, Max 100
homing_retract_dist: 5
homing_positive_dir: true

[tmc2209 stepper_x]
uart_pin: PA3
tx_pin: PA2
uart_address: 0
interpolate: True
run_current: 0.85
hold_current: 0.5
sense_resistor: 0.110
stealthchop_threshold: 999999 #250            # Set to 999999 to turn stealthchop on, and 0 to use spreadcycle

[stepper_y]
step_pin: PC14
## Refer to https://docs.vorondesign.com/build/startup/#v0
dir_pin: PC13
enable_pin: !PC15
rotation_distance: 40
microsteps: 16
endstop_pin: ^PC8
position_endstop: 120
position_max: 120
homing_speed: 20                              # Can be increased after initial setup, Max 100
homing_retract_dist: 5
homing_positive_dir: true

[tmc2209 stepper_y]
uart_pin: PA3
tx_pin: PA2
uart_address: 2
interpolate: True
run_current: 0.85                             # For V0.1 spec NEMA14 40Ncm
hold_current: 0.5
sense_resistor: 0.110
stealthchop_threshold: 99999 #250             # Set to 999999 to turn stealthchop on, and 0 to use spreadcycle

#####################################################################
#   Z Stepper Settings
#####################################################################

[stepper_z]
step_pin: PB9
dir_pin: !PB8	# Remove ! if moving opposite direction
enable_pin: !PC2
rotation_distance: 8 #for T8x8 lead screw
#rotation_distance: 2 #for T8x2 lead screw
microsteps: 16
endstop_pin: ^PB1
#position_endstop: -.10
position_max: 120
position_min: -1.5
homing_speed: 10   #Max 100
second_homing_speed: 3.0
homing_retract_dist: 3.0

[tmc2209 stepper_z]
uart_pin: PA3
tx_pin: PA2
uart_address: 1
interpolate: True
run_current: 0.37                              # For V0.1 spec NEMA17 w/ integrated lead screw
hold_current: 0.35
sense_resistor: 0.110
stealthchop_threshold: 500                     # Set to 999999 to turn stealthchop on, and 0 to use spreadcycle

#####################################################################
#   Extruder
#####################################################################

[extruder]
step_pin: PB2
dir_pin: PA15	                     # Add ! if moving opposite direction
enable_pin: !PD2
full_steps_per_rotation: 200         # 1.8 degree motor
rotation_distance: 22.23             # See calibrating rotation_distance on extruders doc
gear_ratio: 50:10                    # For Mini Afterburner
microsteps: 16
nozzle_diameter: 0.400
filament_diameter: 1.750
heater_pin: PC6
sensor_type: Generic 3950
sensor_pin: PC4
control: pid                         # Do PID calibration
pid_Kp: 28.182
pid_Ki: 1.978
pid_Kd: 100.397
min_temp: 0
max_temp: 270
min_extrude_temp: 170
max_extrude_only_distance: 780.0
max_extrude_cross_section: 0.8
pressure_advance: 0.0                 # See tuning pressure advance doc
pressure_advance_smooth_time: 0.040

[tmc2209 extruder]
uart_pin: PA3
tx_pin: PA2
uart_address: 3
interpolate: True
run_current: 0.35
hold_current: 0.2
sense_resistor: 0.110
stealthchop_threshold: 500

[heater_bed]
heater_pin: PC7
sensor_type: NTC 100K beta 3950         # Verify yours
#sensor_type: NTC 100K MGB18-104F39050L32
sensor_pin: PC5
smooth_time: 3.0
#max_power: 0.6                         # Only need this for 100w pads
min_temp: 0
max_temp: 120
control: pid                            # Do PID calibration
pid_kp: 68.453
pid_ki: 2.749
pid_kd: 426.122



[heater_fan hotend_fan]
# FAN1 Connector
pin: PA13
max_power: 1.0
kick_start_time: 0.5
heater: extruder
heater_temp: 50.0
#fan_speed: 1.0                         # You can't PWM the delta fan unless using blue wire


[fan]
# Print Cooling Fan: FAN0 Connector
pin: PA14
max_power: 1.0
kick_start_time: 0.5
#depending on your fan, you may need to increase or reduce this value
#if your fan will not start
#off_below: 0.13
cycle_time: 0.010

[idle_timeout]
timeout: 1800

[board_pins]
aliases:
    # EXP1 header
    EXP1_1=<5V>,  EXP1_3=<RST>, EXP1_5=PA7,  EXP1_7=PA4,  EXP1_9=PA5,
    EXP1_2=<GND>, EXP1_4=PC3,   EXP1_6=PC11, EXP1_8=PC10, EXP1_10=PA6,

    # EXP2 header
    EXP2_1=<5V>,  EXP2_3=PB7, EXP2_5=PB14, EXP2_7=PB12, EXP2_9=PC12,
    EXP2_2=<GND>, EXP2_4=PB6, EXP2_6=PB13, EXP2_8=PB15, EXP2_10=PC9,

    # EXP3 header
    EXP3_1=PC9,  EXP3_3=PC10, EXP3_5=PC11, EXP3_7=PB12, EXP3_9=<GND>,
    EXP3_2=PC12, EXP3_4=PB14, EXP3_6=PB13, EXP3_8=PB15, EXP3_10=<5V>
    # Pins EXP3_4, EXP3_8, EXP3_6 are also MISO, MOSI, SCK of bus "spi2"


[safe_z_home]
home_xy_position: 120,120
speed: 50.0
z_hop: 5

# Tool to help adjust bed leveling screws. One may define a
# [bed_screws] config section to enable a BED_SCREWS_ADJUST g-code
# command.
[bed_screws]
screw1: 65,5
screw1_name: front screw
screw2: 10,110
screw2_name: back left
screw3: 120,110
screw3_name: back right

#####################################################################
#	Macros
#####################################################################

[gcode_macro PRINT_START]
#   Use PRINT_START for the slicer starting script - please customize for your slicer of choice
gcode:
    G28                            ; home all axes
    G1 Z20 F3000                   ; move nozzle away from bed
   
[gcode_macro PRINT_END]
#   Use PRINT_END for the slicer ending script - please customize for your slicer of choice
gcode:

    M400                           ; wait for buffer to clear
    G92 E0                         ; zero the extruder
    G1 E-4.0 F3600                 ; retract filament
    G91                            ; relative positioning

    #   Get Boundaries
    {% set max_x = printer.configfile.config["stepper_x"]["position_max"]|float %}
    {% set max_y = printer.configfile.config["stepper_y"]["position_max"]|float %}
    {% set max_z = printer.configfile.config["stepper_z"]["position_max"]|float %}

    #   Check end position to determine safe direction to move
    {% if printer.toolhead.position.x < (max_x - 20) %}
        {% set x_safe = 20.0 %}
    {% else %}
        {% set x_safe = -20.0 %}
    {% endif %}

    {% if printer.toolhead.position.y < (max_y - 20) %}
        {% set y_safe = 20.0 %}
    {% else %}
        {% set y_safe = -20.0 %}
    {% endif %}

    {% if printer.toolhead.position.z < (max_z - 2) %}
        {% set z_safe = 2.0 %}
    {% else %}
        {% set z_safe = max_z - printer.toolhead.position.z %}
    {% endif %}

    G0 Z{z_safe} F3600    ; move nozzle up
    G0 X{x_safe} Y{y_safe} F20000    ; move nozzle to remove stringing
    TURN_OFF_HEATERS
    M107                           ; turn off fan
    G90                            ; absolute positioning
    G0 X60 Y{max_y} F3600          ; park nozzle at rear
	
[gcode_macro LOAD_FILAMENT]
gcode:
   M83                            ; set extruder to relative
   G1 E30 F300                    ; load
   G1 E15 F150                    ; prime nozzle with filament
   M82                            ; set extruder to absolute
    
[gcode_macro UNLOAD_FILAMENT]
gcode:
   M83                            ; set extruder to relative
   G1 E10 F300                    ; extrude a little to soften tip
   G1 E-40 F1800                  ; retract some, but not too much or it will jam
   M82                            ; set extruder to absolute

#[include v0_display.cfg]
#[include bedScrewMenu.cfg]

# Sensor Types
#   "EPCOS 100K B57560G104F"
#   "ATC Semitec 104GT-2"
#   "NTC 100K beta 3950" (Keenovo Heater Pad)
#   "Honeywell 100K 135-104LAG-J01"
#   "NTC 100K MGB18-104F39050L32"
#   "AD595"
#   "PT100 INA826"
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

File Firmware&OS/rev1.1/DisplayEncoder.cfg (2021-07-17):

# See the sample-lcd.cfg file for definitions of common LCD displays.
[mcu displayEncoder]
serial: /dev/serial/by-id/usb-Klipper_stm32f042x6_0B0008000743535031303420-if00
restart_method: command

[display]
lcd_type: sh1106
i2c_mcu: displayEncoder
i2c_bus: i2c1a
encoder_pins: ^displayEncoder:PA4, ^displayEncoder:PA3
click_pin: ^!displayEncoder:PA1
kill_pin: ^!displayEncoder:PA5

[neopixel displayStatus]
pin: displayEncoder:PA0
chain_count: 1
color_order: GRB
initial_RED: 0.2
initial_GREEN: 0.05
initial_BLUE: 0

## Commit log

2021-07-17 Upload firmware related stuff
    [printer.cfg, stm32_mini12864.cfg]
2021-07-21 Upload bedScrewMenu.cfg
    [bedScrewMenu.cfg, printer.cfg]
2021-07-22 Update product information
    Upload product information, update readme
    [2mm_Bottom_Corner_Front_x1.STL, 2mm_Bottom_Corner_Rear_mirror_x1.STL, 2mm_Bottom_Corner_Rear_x1.STL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]
2021-07-29 Update README for STM32_Mini12864
2021-07-29 Update for v0 display
    [DisplayEncoder.cfg, printer.cfg]
2021-08-23 Change wiring location
2021-08-23 Update wiring information
2021-08-25 Add Tornado hotend features
2021-09-11 Add machined parts kit information
    [Hotbed_wire_harness_clamp.STL, rear_right_foot.STL]
2021-09-11 Add wiring sample
2021-09-11 Update wiring sample jpg
2021-09-25 Update tornado hotend readme
2021-10-23 Upload BOM
2021-10-28 Update BOM
2021-11-27 Add Tornado hotend installation guide
2021-12-10 Upload OctoPi OS
    [DisplayEncoder.cfg, bedScrewMenu.cfg, printer.cfg]
2021-12-22 Add rev1.1 kit
    [DisplayEncoder.cfg, bedScrewMenu.cfg, fysetc cheetah 2 for voron 0.1.cfg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]
2021-12-22 Update rev1.1 wiring
2021-12-23 Add rev1.1 kit bom
2022-08-04 Update to latest klipper and add mainsail os support
2022-08-23 Update thermistor type
    [printer.cfg]
2022-12-06 Update BOM
    Update V1.2 V1.3 BOM
